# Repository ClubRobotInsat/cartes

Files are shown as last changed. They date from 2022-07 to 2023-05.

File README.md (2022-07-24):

# Cartes du club robot

Toutes les cartes ici sont les cartes en développement au club. Vous pouvez retrouver
dans les release les cartes correspondant à chaque robot.

Dans le dossier `manufactured` vous pouvez retrouver toutes les cartes qui ont été fabriquées. Elles sont
identifiées par un code unique que vous pouvez retrouver sur le PCB.

## Procédure de fabrication

Lorsque vous envoyez une carte à fabriquer, il faut:
- Ajouter un identifiant à la carte (de la forme `[A-Z]{3}`)
- Copier le projet dans le dossier `manufactured`
- Renommer le projet en `[identifiant] {nom}`

Cela permet d'avoir une trace exacte de toutes les cartes fabriquées. Une carte dans le dossier `manufactured` n'est pas
forcément définitive, mais cela permet d'identifier les cartes que nous pouvons trouver dans le local.

## Procédure post-coupe

Lorsque la coupe est finie il faut produire une release contenant toutes les cartes utilisées, c'est pratique pour comprendre
comment fonctionnait le robot.

## Cartes

### Alimentation

Carte principale d'alimentation du robot, adapte la tension batterie pour alimenter les différets composants.

### Base roulante

Carte pour la gestion de la base roulante du robot

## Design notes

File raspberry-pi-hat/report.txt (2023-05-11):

Plotted to '/home/joel/Documents/Code/Club_Robot/cartes/raspberry-pi-hat/raspberry-pi-hat-F_Cu.gbr'.
Plotted to '/home/joel/Documents/Code/Club_Robot/cartes/raspberry-pi-hat/raspberry-pi-hat-B_Cu.gbr'.
Plotted to '/home/joel/Documents/Code/Club_Robot/cartes/raspberry-pi-hat/raspberry-pi-hat-Edge_Cuts.gbr'.
Created Gerber job file '/home/joel/Documents/Code/Club_Robot/cartes/raspberry-pi-hat/raspberry-pi-hat-job.gbrjob'.
Info: Done.

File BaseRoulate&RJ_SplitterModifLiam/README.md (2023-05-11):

# Modif Base Roulante

Suppression d'un via (pour eviter le meme probleme qu'avec la precedente carte)
Rajout de texte, pour meilleure lisibilité
Rajout d'une piste oubliée
Sinon tout à l'air bien

# Modif RJ Splitter

Connexion de tous les +5V
Sinon tout à l'air OK (pour l'instant...)

# Modif carteIO 
Piste oubliée
Via qui me semblait pas être utile étant donné les deux plans de masses correctement mis en place
Probleme : les erreurs d'empreinte des Packs GPIO, je ne sais pas ce que c'est pour l'instant

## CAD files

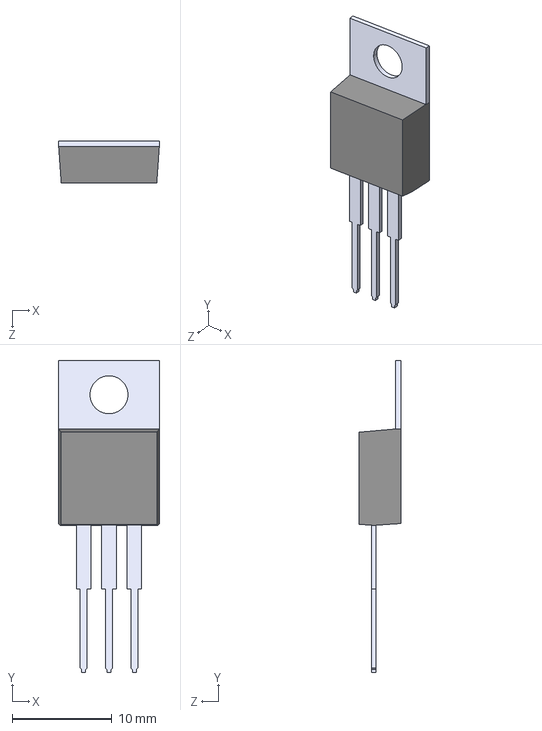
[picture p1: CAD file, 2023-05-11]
BaseRoulate&RJ_SplitterModifLiam/carteIOModifLiam/LM317T_NOPB.step
10.2 x 31.2 x 4.20 mm

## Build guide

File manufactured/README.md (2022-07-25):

| Identifiant | Année | Nom |
|---|---|---|
| AAA |  2022 | Alimentation principale |
| AAB |  2022 | Base roulante |

# Utilité des cartes

## AAA - Alimentation principale

Première version de la carte principale d'alimentation pour le robot. Elle s'alimente avec la batterie et produit du 5V et du 12V régulé. Elle sert également de bouchon pour le bus can.

## AAB - Base roulante

Première version de la base roulante, qui utilse les pont en H makerbot.

## AAC - Prototypage LMD18200

Petit module pour prototyper le module LMD18200 sur breadboard.

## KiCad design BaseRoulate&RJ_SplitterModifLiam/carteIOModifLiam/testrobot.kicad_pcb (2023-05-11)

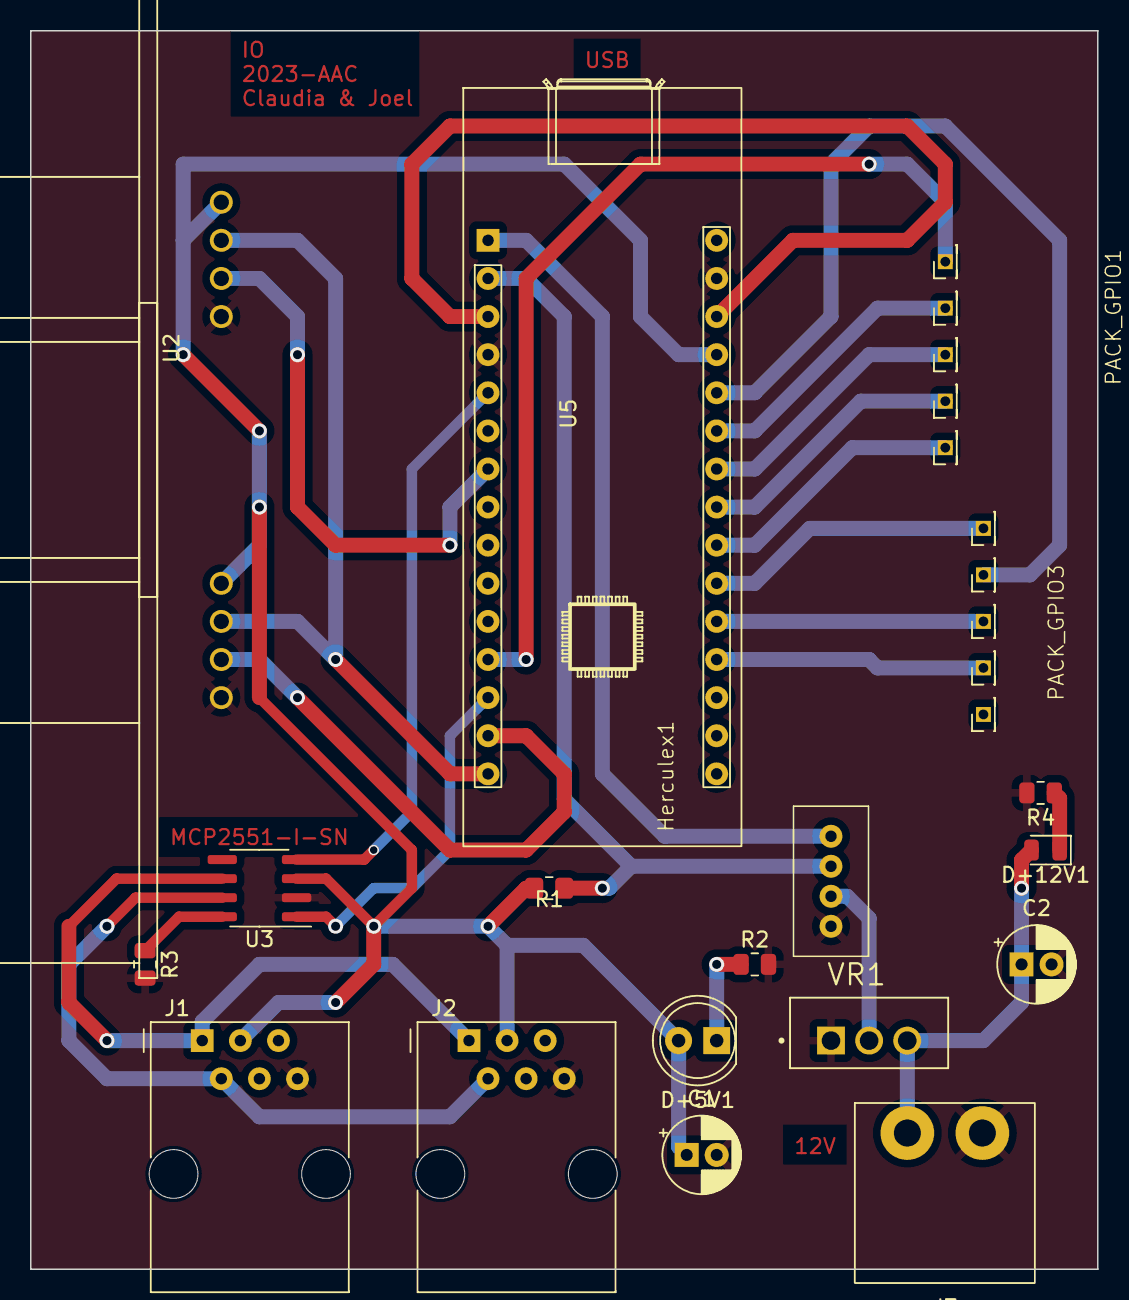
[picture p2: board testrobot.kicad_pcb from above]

Board: 2 copper layers, 71.1 x 82.6 mm, 19 parts (0 on the bottom side), 26 nets.

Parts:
C1: C_Polarized; CP_Radial_D5.0mm_P2.00mm
C2: 470u; CP_Radial_D5.0mm_P2.00mm
D+5V1: LED; LED_D5.0mm
D+12V1: LED bleu; LED_0805_2012Metric
Herculex1: herculex
J1, J2: RJ_can; RJ12
J3: connector_power; WR_TBL_3137_2pins
PACK_GPIO1, PACK_GPIO3: gpio
R1: 4700; R_0805_2012Metric_Pad1.20x1.40mm_HandSolder
R2, R3: R; R_0805_2012Metric
R4: 1k; R_0805_2012Metric
U1, U2: HC-SR04; XCVR_HC-SR04
U3: MCP2551-I-SN; SOIC-8_3.9x4.9mm_P1.27mm
U5: Nucleo_STM32G431KB
VR1: LM317T/NOPB; TO254P1054X470X1955-3

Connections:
+5V: C1.1, D+5V1.2 (A), J1.3 (+5V), J2.3 (+5V), R1.1, U1.1 (VCC), U2.1 (VCC), U3.3 (VDD), U5.27 (+5V)
+8V: Herculex1.2 (+8V), VR1.2 (VOUT)
+12V: C2.1, D+12V1.2 (A), J3.1 (+12V), VR1.3 (VIN)
CANH: J1.2 (CANH), J2.2 (CANH), U3.7 (CANH)
CANL: J1.1 (CANL), J2.1 (CANL), U3.6 (CANL)
CAN_RX: U3.4 (RXD), U5.5 (PA12)
CAN_TX: U3.1 (TXD), U5.13 (PA11)
Echo_b5: U2.3 (ECHO), U5.14 (PB5)
Echo_b7: U1.3 (ECHO), U5.7 (PB7)
GND: C1.2, C2.2, Herculex1.1 (GND), J1.6 (GND), J2.6 (GND), J3.2 (GND), R2.2, R3.2, R4.2, U1.4 (GND), U2.4 (GND), U3.2 (VSS), U5.4 (GND), U5.29 (GND), VR1.1 (ADJ)
unnamed: D+5V1.1 (K), R2.1
unnamed: D+12V1.1 (K), R4.1
unnamed: R3.1, U3.8 (Rs)
unnamed: U5.3 (~RST), U5.28 (~RST)
PA0: PACK_GPIO3.2 (GPIO2), U5.19 (PA0)
PA1: PACK_GPIO3.3 (GPIO3), U5.20 (PA1)
PA2: PACK_GPIO3.4 (GPIO4), U5.26 (PA2)
PA3: PACK_GPIO3.5 (GPIO5), U5.21 (PA3)
PA4: PACK_GPIO1.1 (GPIO1), U5.22 (PA4)
PA5: PACK_GPIO1.2 (GPIO2), U5.23 (PA5/PB7)
PA6: PACK_GPIO1.3 (GPIO3), U5.24 (PA6/PA15)
PA7: PACK_GPIO1.4 (GPIO4), U5.25 (PA7)
PA8: PACK_GPIO1.5 (GPIO5), U5.12 (PA8)
RX_Hercu: Herculex1.4 (RX), U5.1 (PA9)
TX_Herculex: Herculex1.3 (TX), R1.2, U5.2 (PA10)
Trig_b4: U1.2 (TRIG), U2.2 (TRIG), U5.15 (PB4)

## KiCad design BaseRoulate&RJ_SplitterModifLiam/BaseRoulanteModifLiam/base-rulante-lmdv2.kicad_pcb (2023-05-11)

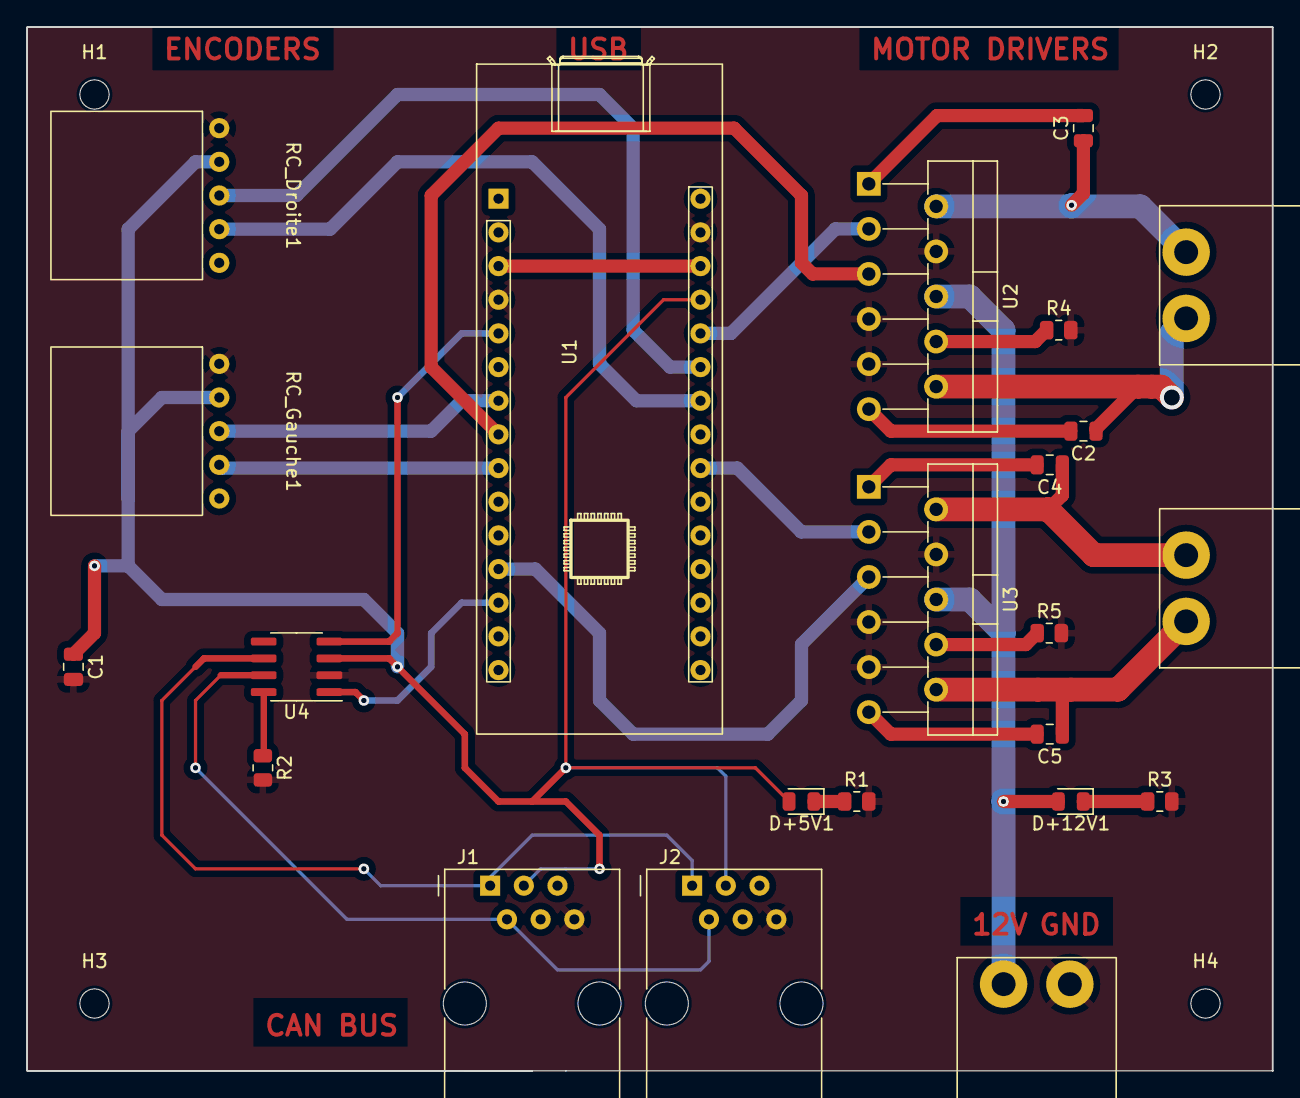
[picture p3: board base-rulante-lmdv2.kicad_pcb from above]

Board: 2 copper layers, 94.0 x 78.7 mm, 27 parts (0 on the bottom side), 29 nets.

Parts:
C1, C2, C3, C4, C5: C_Polarized; C_0805_2012Metric
D+5V1, D+12V1: LED; LED_0805_2012Metric
H1, H2, H3, H4: MountingHole; MountingHole_2.2mm_M2
J1, J2: RJ_can; RJ12
J3, J4, J5: connector_power; WR_TBL_3137_2pins
R1, R2, R3, R4, R5: R; R_0805_2012Metric
RC_Droite1: roues_codeuses; HE14-5-angle
RC_Gauche1: roues_codeuses; HE14-5-angle
U1: Nucleo_STM32G431KB
U2, U3: LMD18200; TO-220-11_P3.4x5.08mm_StaggerOdd_Lead4.85mm_Vertical
U4: MCP2551-I-SN; SOIC-8_3.9x4.9mm_P1.27mm

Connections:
+5V: C1.1, D+5V1.2 (A), J1.3 (+5V), J2.3 (+5V), RC_Droite1.2 (+5V), RC_Gauche1.2 (+5V), U1.27 (+5V), U4.3 (VDD)
+12V: D+12V1.2 (A), J3.1 (+12V), U2.6 (VS), U3.6 (VS)
A_D: RC_Droite1.3 (A), U1.25 (PA7)
A_G: RC_Gauche1.3 (A), U1.7 (PB7)
B_D: RC_Droite1.4 (B), U1.24 (PA6/PA15)
B_G: RC_Gauche1.4 (B), U1.9 (PB6)
CANH: J1.2 (CANH), J2.2 (CANH), U4.7 (CANH)
CANL: J1.1 (CANL), J2.1 (CANL), U4.6 (CANL)
CAN_RX: U1.5 (PA12), U4.4 (RXD)
CAN_TX: U1.13 (PA11), U4.1 (TXD)
DIR_D: U1.26 (PA2), U2.3 (DIRECTION)
DIR_G: U1.22 (PA4), U3.3 (DIRECTION)
GND: C1.2, J1.6 (GND), J2.6 (GND), J3.2 (GND), R1.2, R2.2, R3.2, R4.2, R5.2, RC_Droite1.1 (GND), RC_Gauche1.1 (GND), U1.4 (GND), U1.29 (GND), U2.4 (BRAKE), U2.7 (GND), U2.9 (~THERMAL_FLAG_OUTPUT), U3.4 (BRAKE), U3.7 (GND), U3.9 (~THERMAL_FLAG_OUTPUT), U4.2 (VSS)
Mot_D_Out1: C3.1, J4.2 (GND), U2.2 (OUTPUT1)
Mot_D_Out2: C2.1, J4.1 (+12V), U2.10 (OUTPUT2)
Mot_G_Out1: C4.1, J5.2 (GND), U3.2 (OUTPUT1)
Mot_G_Out2: C5.1, J5.1 (+12V), U3.10 (OUTPUT2)
unnamed: D+5V1.1 (K), R1.1
unnamed: D+12V1.1 (K), R3.1
unnamed: U1.3 (~RST), U1.28 (~RST)
unnamed: C3.2, U2.1 (BOOTSTRAP1)
unnamed: C2.2, U2.11 (BOOTSTRAP2)
unnamed: R4.1, U2.8 (CURRENT_SENSE_OUTPUT)
unnamed: C4.2, U3.1 (BOOTSTRAP1)
unnamed: C5.2, U3.11 (BOOTSTRAP2)
unnamed: R5.1, U3.8 (CURRENT_SENSE_OUTPUT)
unnamed: R2.1, U4.8 (Rs)
PWM_D: U1.8 (PA15), U2.5 (PWM)
PWM_G: U1.12 (PA8), U3.5 (PWM)

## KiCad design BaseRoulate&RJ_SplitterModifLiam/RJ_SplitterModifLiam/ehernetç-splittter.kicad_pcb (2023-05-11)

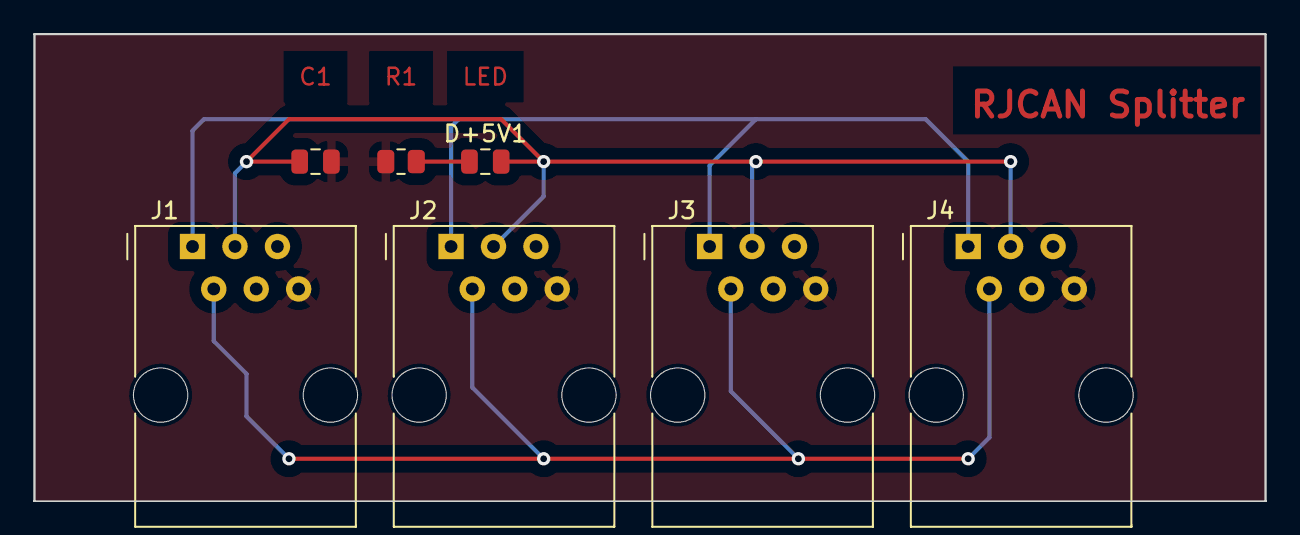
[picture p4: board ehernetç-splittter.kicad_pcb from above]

Board: 2 copper layers, 73.7 x 27.9 mm, 7 parts (0 on the bottom side), 5 nets.

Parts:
C1: C_Polarized; C_0805_2012Metric
D+5V1: LED; C_0805_2012Metric
J1, J2, J3, J4: RJ_can; RJ12
R1: R; R_0805_2012Metric

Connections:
+5V: C1.1, D+5V1.2 (A), J1.3 (+5V), J2.3 (+5V), J3.3 (+5V), J4.3 (+5V)
CANH: J1.2 (CANH), J2.2 (CANH), J3.2 (CANH), J4.2 (CANH)
CANL: J1.1 (CANL), J2.1 (CANL), J3.1 (CANL), J4.1 (CANL)
GND: C1.2, J1.6 (GND), J2.6 (GND), J3.6 (GND), J4.6 (GND), R1.2
unnamed: D+5V1.1 (K), R1.1

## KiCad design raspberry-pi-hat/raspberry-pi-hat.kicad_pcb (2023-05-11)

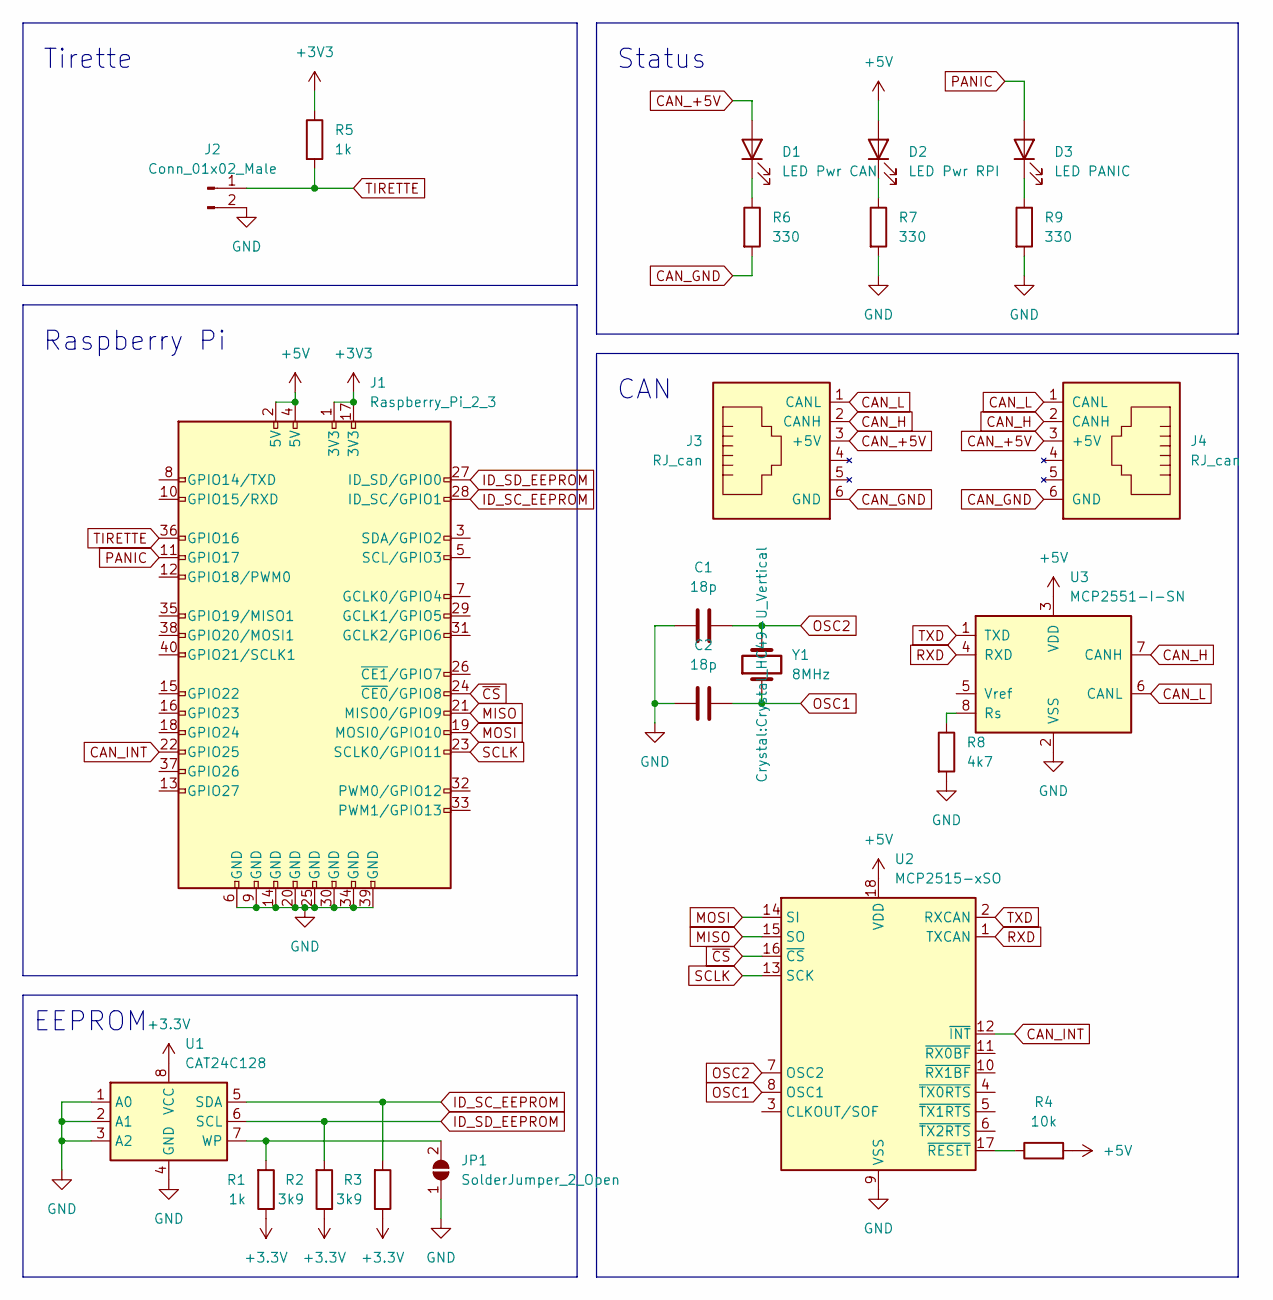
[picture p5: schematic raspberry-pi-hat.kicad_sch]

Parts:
C1, C2: 18p; C_0805_2012Metric
D1: LED Pwr CAN; LED_0805_2012Metric
D2: LED Pwr RPI; LED_0805_2012Metric
D3: LED PANIC; LED_0805_2012Metric
J1: Raspberry_Pi_2_3; PinHeader_2x20_P2.54mm_Vertical
J2: Conn_01x02_Male; PinHeader_1x02_P2.54mm_Horizontal
J3, J4: RJ_can; RJ12
JP1: SolderJumper_2_Open; SolderJumper-2_P1.3mm_Open_TrianglePad1.0x1.5mm
R1, R5: 1k; R_0805_2012Metric
R2, R3: 3k9; R_0805_2012Metric
R4: 10k; R_0805_2012Metric
R6, R7, R9: 330; R_0805_2012Metric
R8: 4k7; R_0805_2012Metric
U1: CAT24C128; SOIC-8_3.9x4.9mm_P1.27mm
U2: MCP2515-xSO; SOIC-18W_7.5x11.6mm_P1.27mm
U3: MCP2551-I-SN; SOIC-8_3.9x4.9mm_P1.27mm
Y1: 8MHz; Crystal_HC49-U_Vertical

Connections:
+3.3V: R1.1, R2.1, R3.1, U1.8 (VCC)
+3V3: J1.1 (3V3), J1.17 (3V3), R5.1
+5V: D2.2 (A), J1.2 (5V), J1.4 (5V), R4.2, U2.18 (VDD), U3.3 (VDD)
CAN_+5V: D1.2 (A), J3.3 (+5V), J4.3 (+5V)
CAN_GND: J3.6 (GND), J4.6 (GND), R6.2
CAN_H: J3.2 (CANH), J4.2 (CANH), U3.7 (CANH)
CAN_INT: J1.22 (GPIO25), U2.12 (~INT)
CAN_L: J3.1 (CANL), J4.1 (CANL), U3.6 (CANL)
GND: C1.2, C2.1, J1.6 (GND), J1.9 (GND), J1.14 (GND), J1.20 (GND), J1.25 (GND), J1.30 (GND), J1.34 (GND), J1.39 (GND), J2.2, JP1.1 (A), R7.2, R8.2, R9.2, U1.1 (A0), U1.2 (A1), U1.3 (A2), U1.4 (GND), U2.9 (VSS), U3.2 (VSS)
ID_SC_EEPROM: J1.28 (ID_SC/GPIO1), R3.2, U1.5 (SDA)
ID_SD_EEPROM: J1.27 (ID_SD/GPIO0), R2.2, U1.6 (SCL)
MISO: J1.21 (MISO0/GPIO9), U2.15 (SO)
MOSI: J1.19 (MOSI0/GPIO10), U2.14 (SI)
unnamed: D1.1 (K), R6.1
unnamed: D2.1 (K), R7.1
unnamed: D3.1 (K), R9.1
unnamed: JP1.2 (B), R1.2, U1.7 (WP)
unnamed: R4.1, U2.17 (~RESET)
unnamed: R8.1, U3.8 (Rs)
OSC1: C2.2, U2.8 (OSC1), Y1.1
OSC2: C1.1, U2.7 (OSC2), Y1.2
PANIC: D3.2 (A), J1.11 (GPIO17)
RXD: U2.1 (TXCAN), U3.4 (RXD)
SCLK: J1.23 (SCLK0/GPIO11), U2.13 (SCK)
TIRETTE: J1.36 (GPIO16), J2.1, R5.2
TXD: U2.2 (RXCAN), U3.1 (TXD)
~CS: J1.24 (~CE0/GPIO8), U2.16 (~CS)

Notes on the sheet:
Status
Raspberry Pi
EEPROM
Tirette
CAN

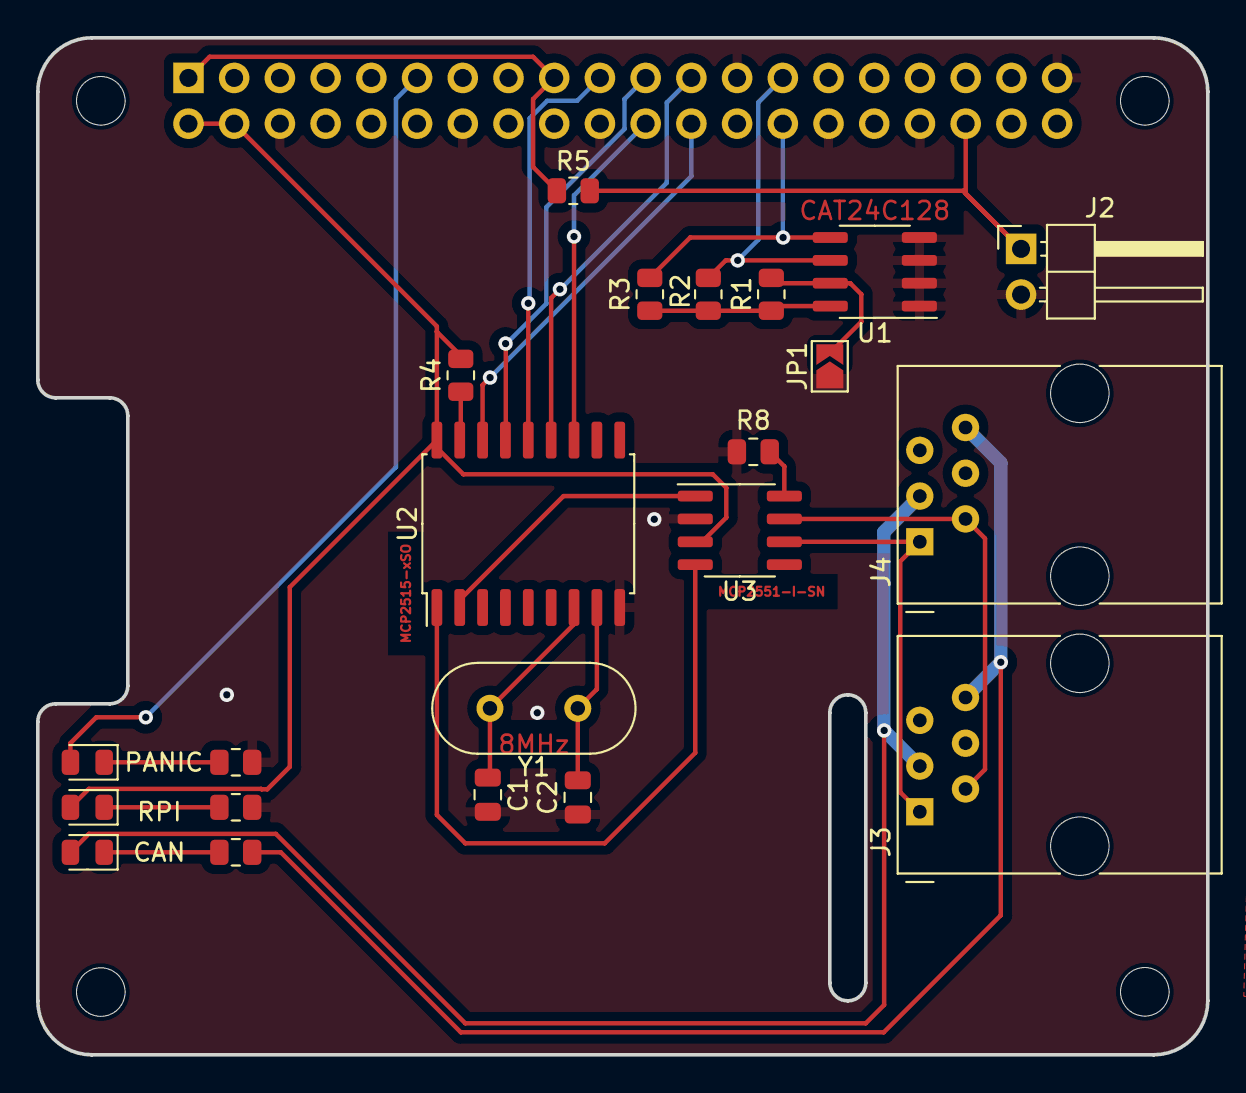
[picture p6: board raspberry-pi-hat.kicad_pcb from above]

Board: 2 copper layers, 65.0 x 56.5 mm, 27 parts (1 on the bottom side), 27 nets.

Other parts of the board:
M1, M2, M3, M4: MountingHole_2.7mm

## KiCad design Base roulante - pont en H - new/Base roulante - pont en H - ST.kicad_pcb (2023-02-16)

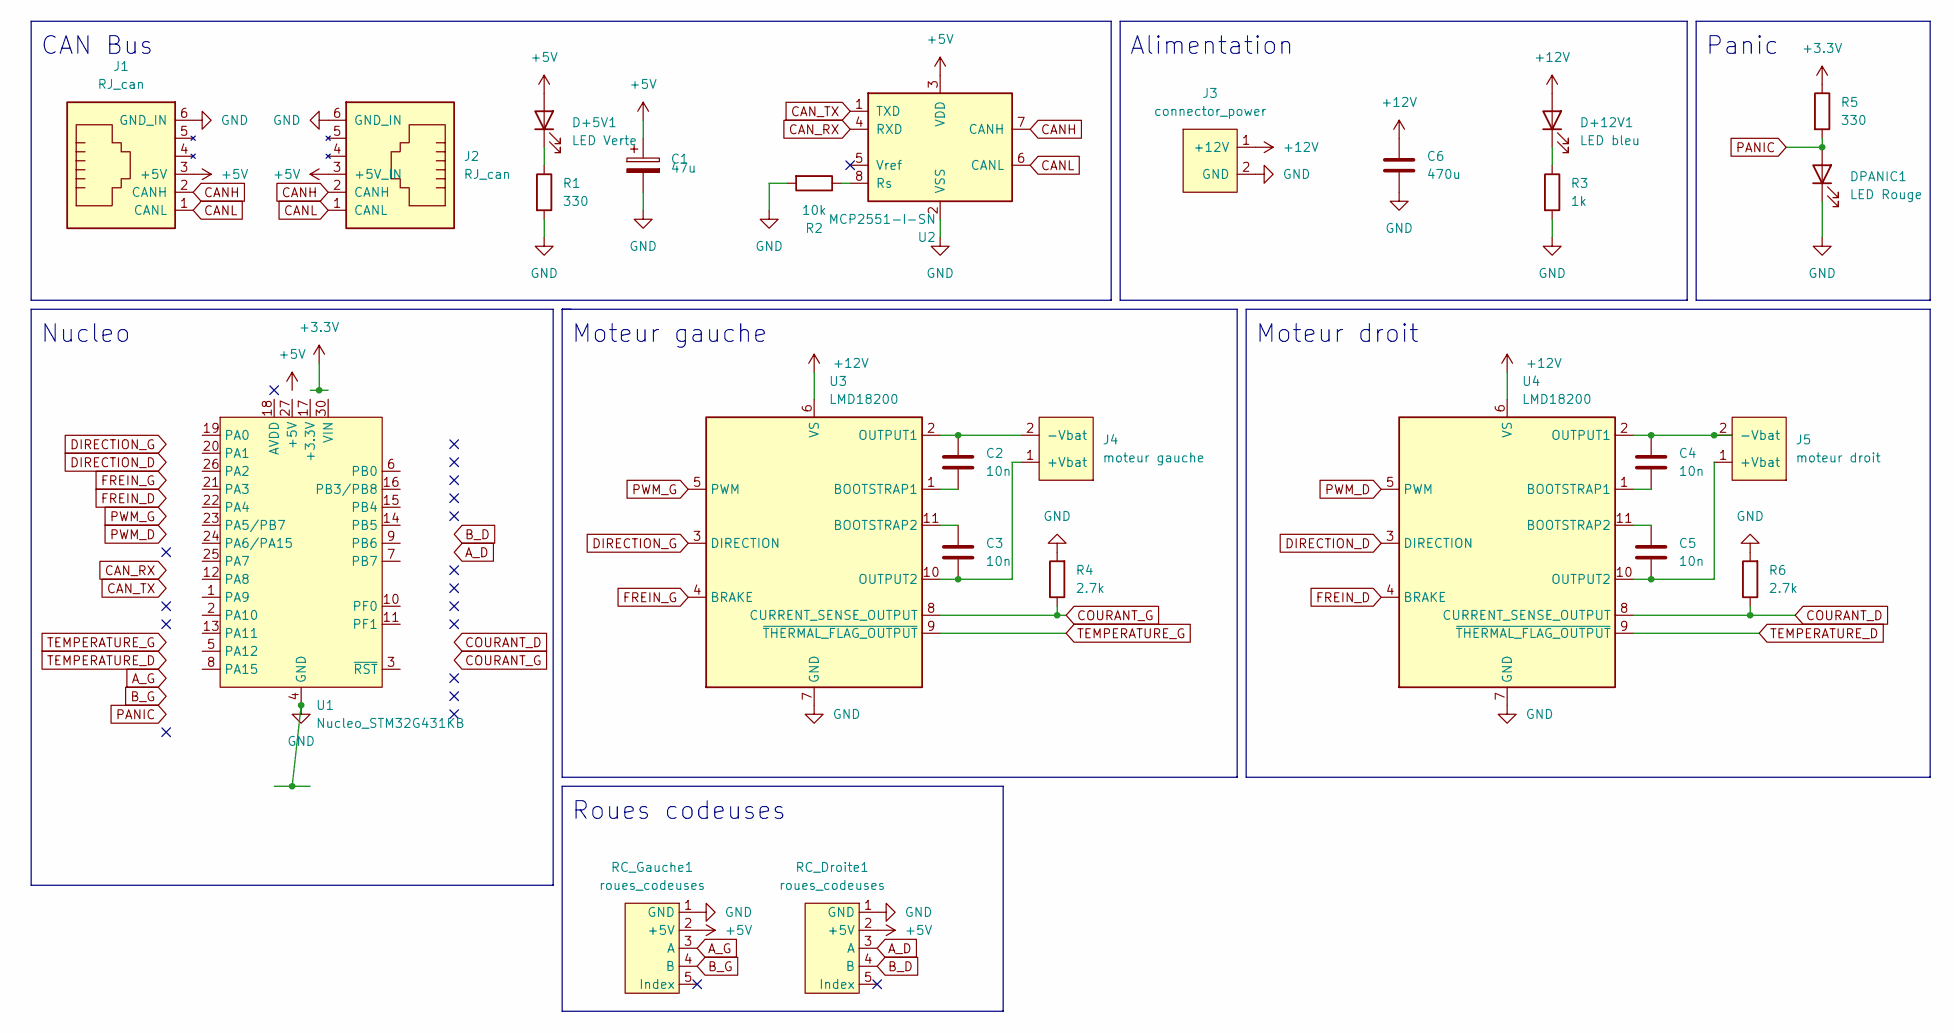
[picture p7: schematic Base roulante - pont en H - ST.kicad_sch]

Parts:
C1: 47u; CP_Radial_D5.0mm_P2.00mm
C2, C3, C4, C5: 10n; C_0805_2012Metric
C6: 470u; CP_Radial_D8.0mm_P3.50mm
D+5V1: LED Verte; LED_0805_2012Metric
D+12V1: LED bleu; LED_0805_2012Metric
DPANIC1: LED Rouge; LED_0805_2012Metric
J1, J2: RJ_can; RJ12
J3: connector_power; WR_TBL_3137_2pins
J4: moteur gauche; WR_TBL_3137_2pins
J5: moteur droit; WR_TBL_3137_2pins
R1, R5: 330; R_0805_2012Metric
R2: 10k; R_0805_2012Metric
R3: 1k; R_0805_2012Metric
R4, R6: 2.7k; R_0805_2012Metric
RC_Droite1: roues_codeuses; HE14-5-angle
RC_Gauche1: roues_codeuses; HE14-5-angle
U1: Nucleo_STM32G431KB
U2: MCP2551-I-SN; SOIC-8_3.9x4.9mm_P1.27mm
U3, U4: LMD18200; TO-220-11_P3.4x5.08mm_StaggerOdd_Lead4.85mm_Vertical

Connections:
+3.3V: R5.1
+5V: C1.1, D+5V1.2 (A), J1.3 (+5V), J2.3 (+5V_IN), RC_Droite1.2 (+5V), RC_Gauche1.2 (+5V), U2.3 (VDD)
+12V: C6.1, D+12V1.2 (A), J3.1 (+12V), U3.6 (VS), U4.6 (VS)
A_D: RC_Droite1.3 (A)
A_G: RC_Gauche1.3 (A)
B_D: RC_Droite1.4 (B)
B_G: RC_Gauche1.4 (B)
CANH: J1.2 (CANH), J2.2 (CANH), U2.7 (CANH)
CANL: J1.1 (CANL), J2.1 (CANL), U2.6 (CANL)
CAN_RX: U2.4 (RXD)
CAN_TX: U2.1 (TXD)
COURANT_D: R6.1, U4.8 (CURRENT_SENSE_OUTPUT)
COURANT_G: R4.1, U3.8 (CURRENT_SENSE_OUTPUT)
DIRECTION_D: U4.3 (DIRECTION)
DIRECTION_G: U3.3 (DIRECTION)
FREIN_D: U4.4 (BRAKE)
FREIN_G: U3.4 (BRAKE)
GND: C1.2, C6.2, DPANIC1.1 (K), J1.6 (GND_IN), J2.6 (GND_IN), J3.2 (GND), R1.2, R2.2, R3.2, R4.2, R6.2, RC_Droite1.1 (GND), RC_Gauche1.1 (GND), U1.4 (GND), U1.29 (GND), U2.2 (VSS), U3.7 (GND), U4.7 (GND)
unnamed: C2.1, J4.2 (-Vbat), U3.2 (OUTPUT1)
unnamed: C2.2, U3.1 (BOOTSTRAP1)
unnamed: C3.1, U3.11 (BOOTSTRAP2)
unnamed: C3.2, J4.1 (+Vbat), U3.10 (OUTPUT2)
unnamed: C4.1, J5.2 (-Vbat), U4.2 (OUTPUT1)
unnamed: C4.2, U4.1 (BOOTSTRAP1)
unnamed: C5.1, U4.11 (BOOTSTRAP2)
unnamed: C5.2, J5.1 (+Vbat), U4.10 (OUTPUT2)
unnamed: D+5V1.1 (K), R1.1
unnamed: D+12V1.1 (K), R3.1
unnamed: R2.1, U2.8 (Rs)
unnamed: U1.3 (~RST), U1.28 (~RST)
PANIC: DPANIC1.2 (A), R5.2
PWM_D: U4.5 (PWM)
PWM_G: U3.5 (PWM)
TEMPERATURE_D: U4.9 (~THERMAL_FLAG_OUTPUT)
TEMPERATURE_G: U3.9 (~THERMAL_FLAG_OUTPUT)

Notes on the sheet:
Panic
Alimentation
CAN Bus
Moteur droit
Roues codeuses
Moteur gauche
Nucleo

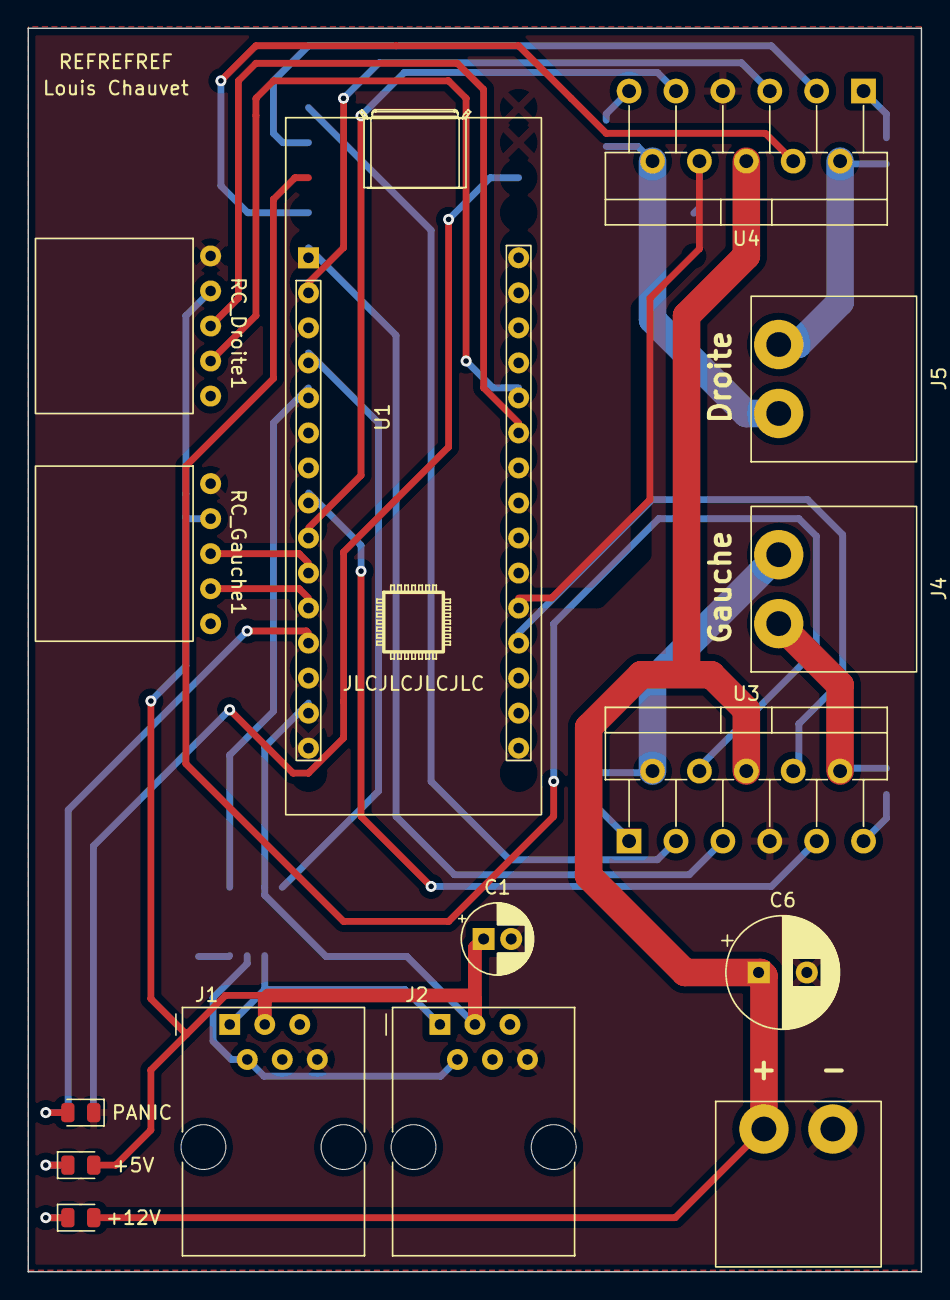
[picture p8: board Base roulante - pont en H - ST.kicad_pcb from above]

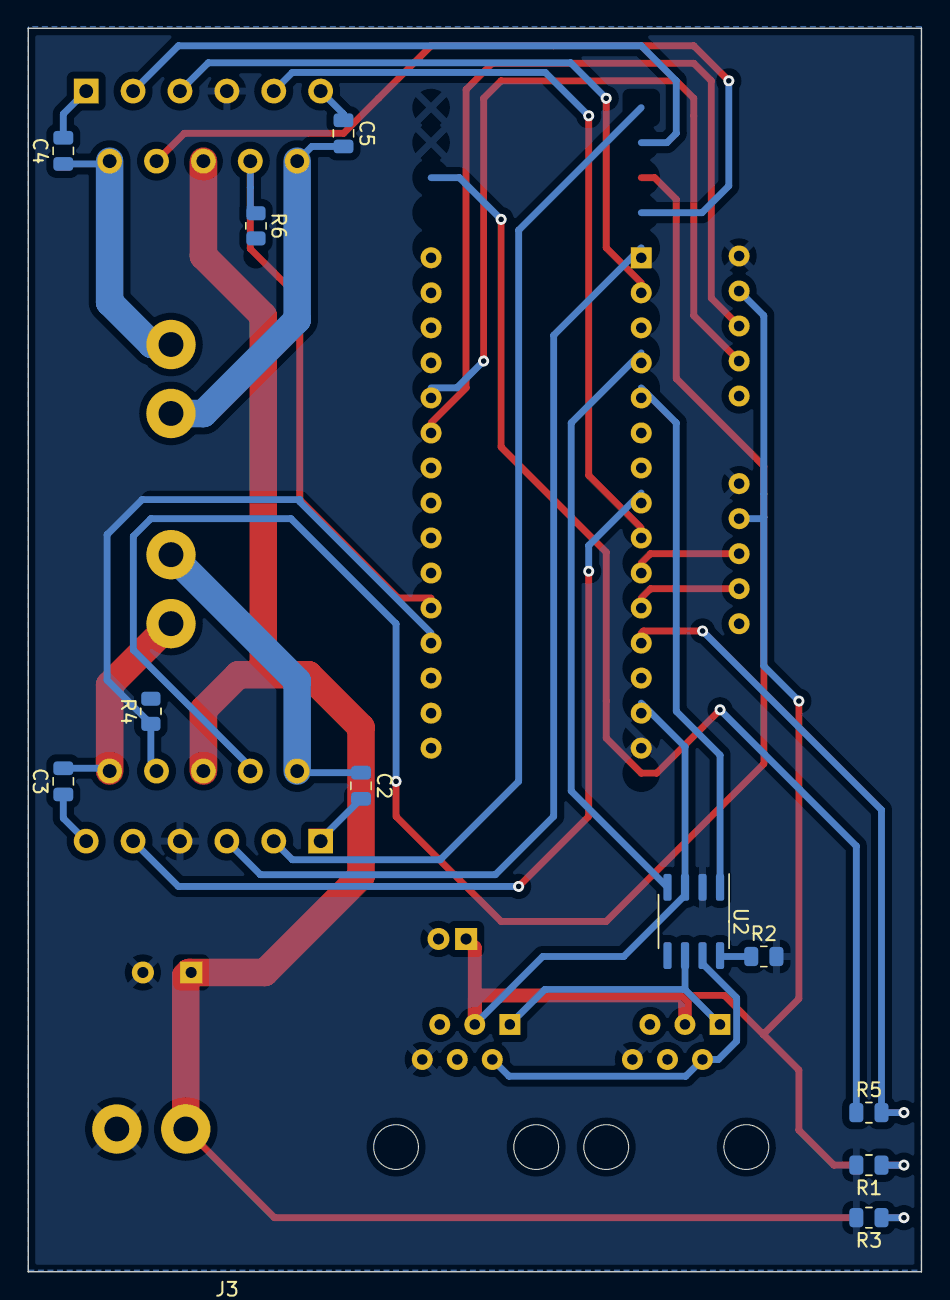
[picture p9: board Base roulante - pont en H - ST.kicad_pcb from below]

Board: 2 copper layers, 64.8 x 90.2 mm, 26 parts (11 on the bottom side), 20 nets.

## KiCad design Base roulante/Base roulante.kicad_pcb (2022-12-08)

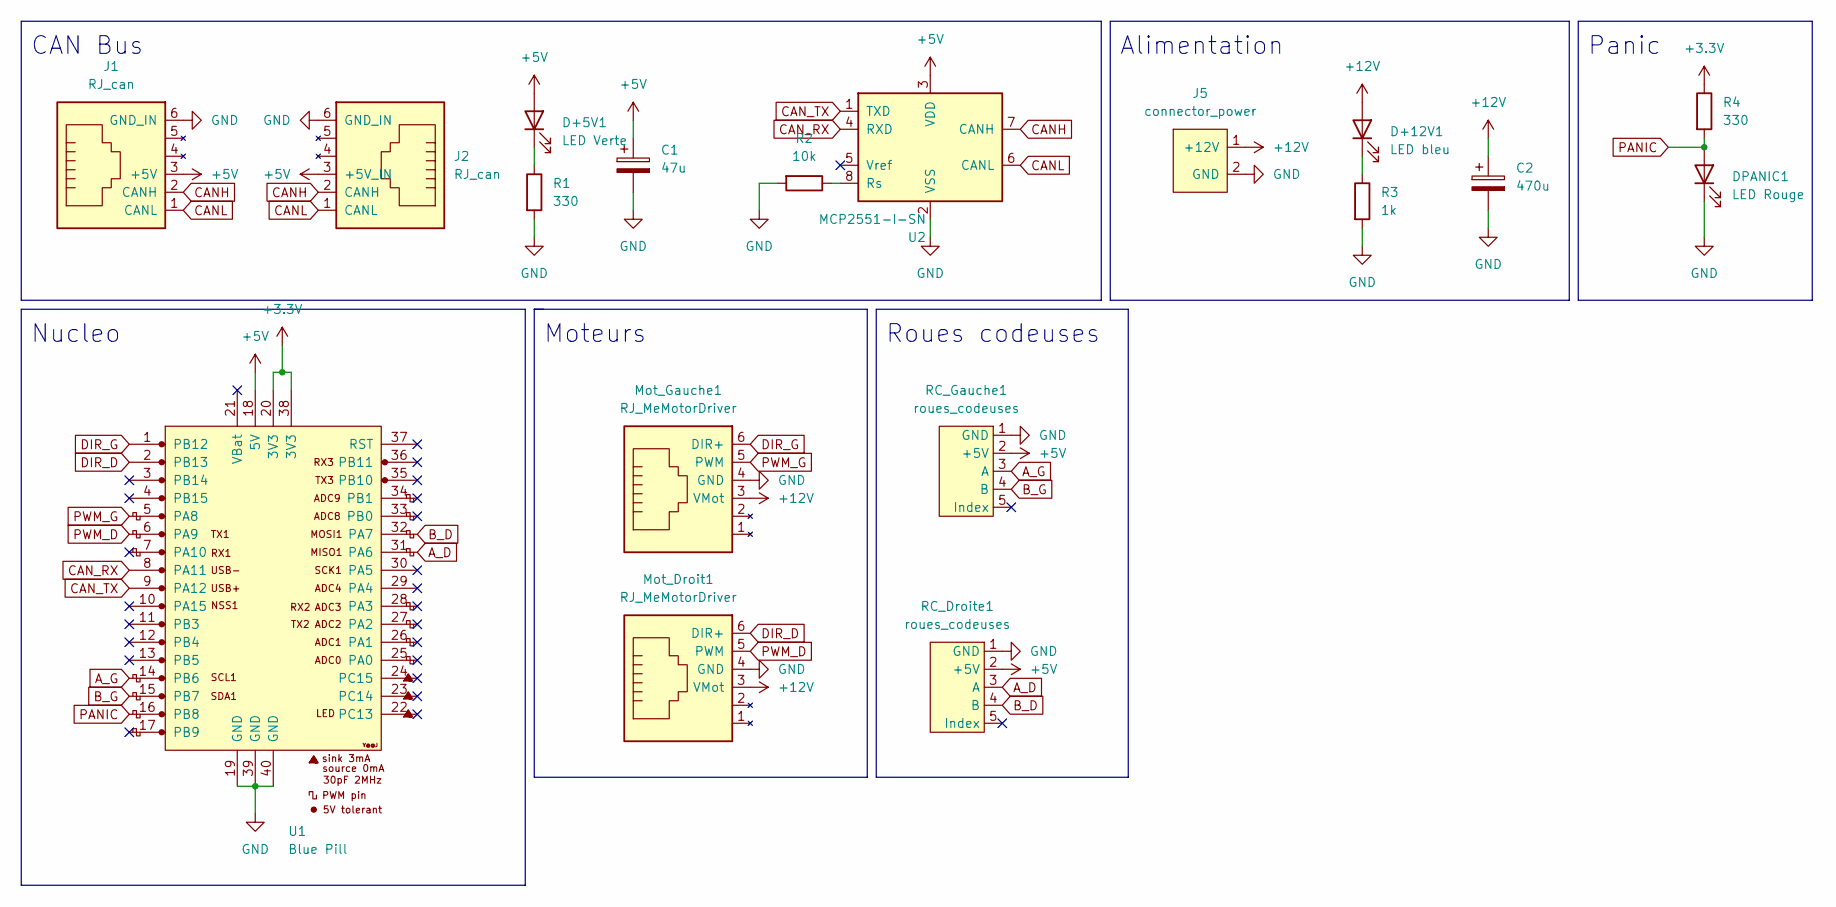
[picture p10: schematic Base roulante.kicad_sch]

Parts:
C1: 47u; CP_Radial_D5.0mm_P2.00mm
C2: 470u; CP_Radial_D5.0mm_P2.00mm
D+5V1: LED Verte; LED_0805_2012Metric
D+12V1: LED bleu; LED_0805_2012Metric
DPANIC1: LED Rouge; LED_0805_2012Metric
J1, J2: RJ_can; RJ12
J5: connector_power; WR_TBL_3137_2pins
Mot_Droit1: RJ_MeMotorDriver; RJ12
Mot_Gauche1: RJ_MeMotorDriver; RJ12
R1, R4: 330; R_0805_2012Metric
R2: 10k; R_0805_2012Metric
R3: 1k; R_0805_2012Metric
RC_Droite1: roues_codeuses; HE14-5-angle
RC_Gauche1: roues_codeuses; HE14-5-angle
U1: Blue Pill
U2: MCP2551-I-SN; SOIC-8_3.9x4.9mm_P1.27mm

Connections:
+3.3V: R4.1, U1.20 (3V3), U1.38 (3V3)
+5V: C1.1, D+5V1.2 (A), J1.3 (+5V), J2.3 (+5V_IN), RC_Droite1.2 (+5V), RC_Gauche1.2 (+5V), U1.18 (5V), U2.3 (VDD)
+12V: C2.1, D+12V1.2 (A), J5.1 (+12V), Mot_Droit1.3 (VMot), Mot_Gauche1.3 (VMot)
A_D: RC_Droite1.3 (A), U1.31 (PA6)
A_G: RC_Gauche1.3 (A), U1.14 (PB6)
B_D: RC_Droite1.4 (B), U1.32 (PA7)
B_G: RC_Gauche1.4 (B), U1.15 (PB7)
CANH: J1.2 (CANH), J2.2 (CANH), U2.7 (CANH)
CANL: J1.1 (CANL), J2.1 (CANL), U2.6 (CANL)
CAN_RX: U1.8 (PA11), U2.4 (RXD)
CAN_TX: U1.9 (PA12), U2.1 (TXD)
DIR_D: Mot_Droit1.6 (DIR+), U1.2 (PB13)
DIR_G: Mot_Gauche1.6 (DIR+), U1.1 (PB12)
GND: C1.2, C2.2, DPANIC1.1 (K), J1.6 (GND_IN), J2.6 (GND_IN), J5.2 (GND), Mot_Droit1.4 (GND), Mot_Gauche1.4 (GND), R1.2, R2.2, R3.2, RC_Droite1.1 (GND), RC_Gauche1.1 (GND), U1.19 (GND), U1.39 (GND), U1.40 (GND), U2.2 (VSS)
unnamed: D+5V1.1 (K), R1.1
unnamed: D+12V1.1 (K), R3.1
unnamed: R2.1, U2.8 (Rs)
PANIC: DPANIC1.2 (A), R4.2, U1.16 (PB8)
PWM_D: Mot_Droit1.5 (PWM), U1.6 (PA9)
PWM_G: Mot_Gauche1.5 (PWM), U1.5 (PA8)

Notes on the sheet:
Alimentation
Nucleo
CAN Bus
Roues codeuses
Panic
Moteurs

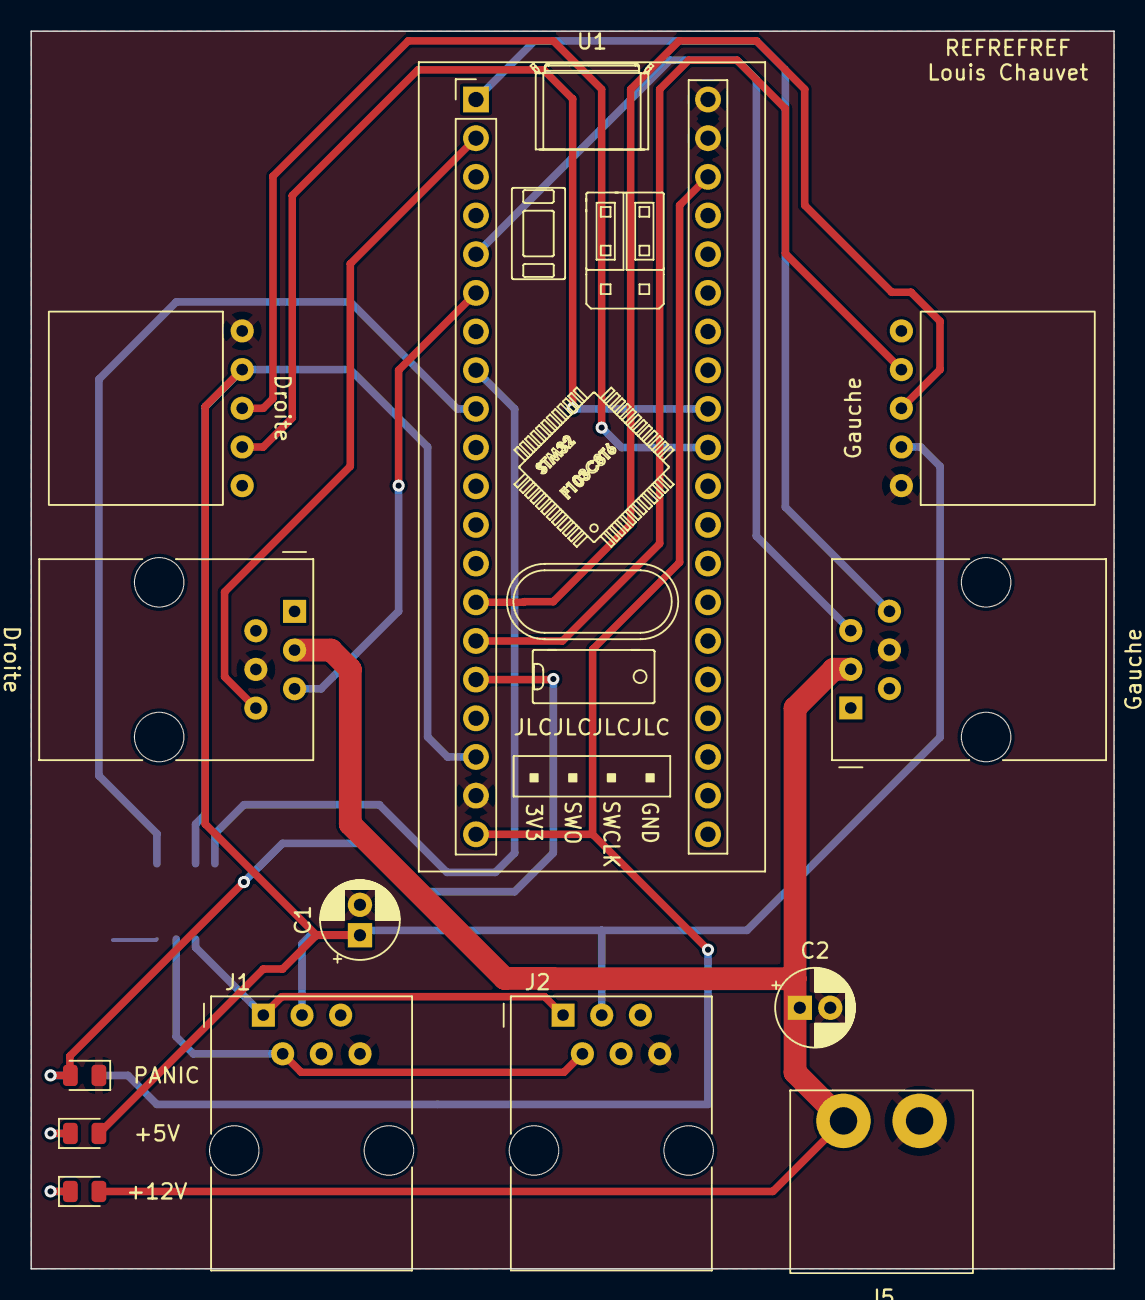
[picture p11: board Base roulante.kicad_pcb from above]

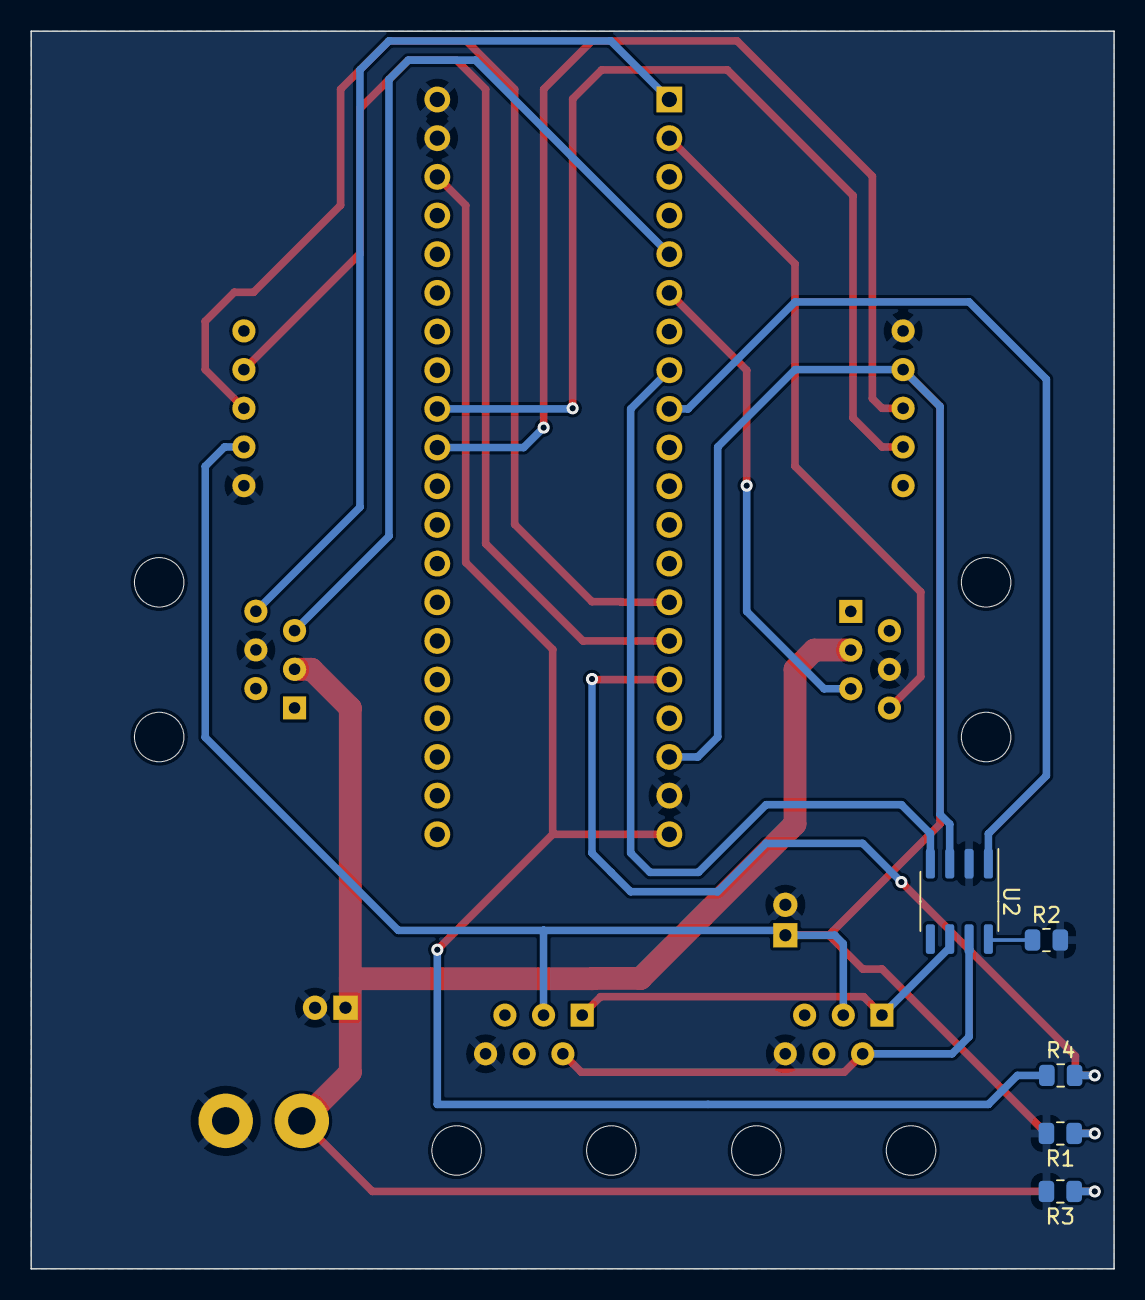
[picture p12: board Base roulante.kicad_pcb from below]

Board: 2 copper layers, 71.1 x 81.3 mm, 18 parts (5 on the bottom side), 20 nets.

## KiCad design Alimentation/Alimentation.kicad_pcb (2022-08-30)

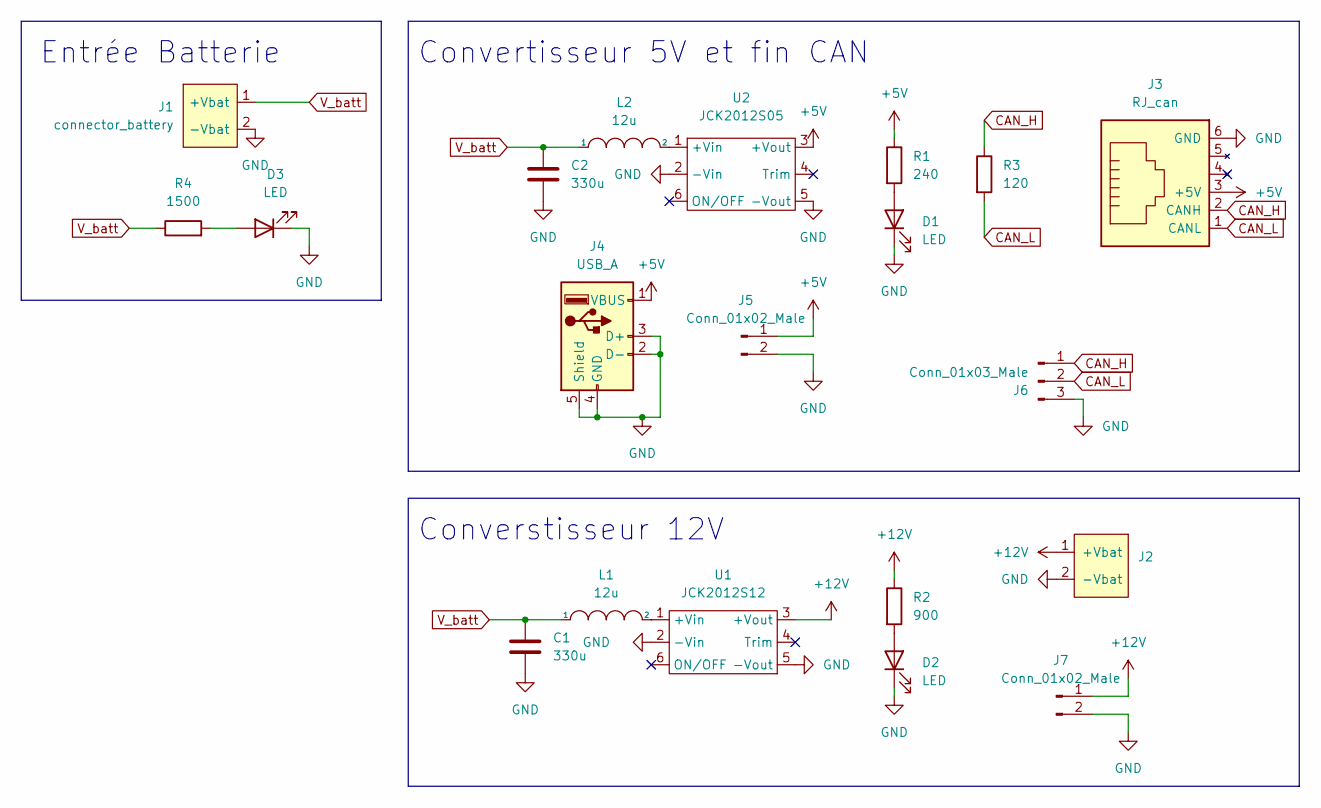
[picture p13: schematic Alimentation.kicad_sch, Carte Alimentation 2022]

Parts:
C1, C2: 330u; CP_Radial_D7.5mm_P2.50mm
D1, D2, D3: LED; LED_D5.0mm
J1: connector_battery; WR_TBL_3137_2pins
J2: WR_TBL_3137_2pins
J3: RJ_can; RJ12
J4: USB_A
J5, J7: Conn_01x02_Male; PinHeader_1x02_P2.54mm_Horizontal
J6: Conn_01x03_Male; PinHeader_1x03_P2.54mm_Horizontal
L1, L2: 12u; L_Radial_D7.8mm_P5.00mm_Fastron_07HCP
R1: 240; R_0805_2012Metric_Pad1.20x1.40mm_HandSolder
R2: 900; R_0805_2012Metric_Pad1.20x1.40mm_HandSolder
R3: 120; R_0805_2012Metric_Pad1.20x1.40mm_HandSolder
R4: 1500; R_0805_2012Metric_Pad1.20x1.40mm_HandSolder
U1: JCK2012S12; JCK
U2: JCK2012S05; JCK

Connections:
+5V: J3.3 (+5V), J4.1 (VBUS), J5.1, R1.1, U2.3 (+Vout)
+12V: J2.1 (+Vbat), J7.1, R2.1, U1.3 (+Vout)
CAN_H: J3.2 (CANH), J6.1, R3.1
CAN_L: J3.1 (CANL), J6.2, R3.2
GND: C1.2, C2.2, D1.1 (K), D2.1 (K), D3.1 (K), J1.2 (-Vbat), J2.2 (-Vbat), J3.6 (GND), J4.2 (D-), J4.3 (D+), J4.4 (GND), J4.5 (Shield), J5.2, J6.3, J7.2, U1.2 (-Vin), U1.5 (-Vout), U2.2 (-Vin), U2.5 (-Vout)
unnamed: D1.2 (A), R1.2
unnamed: D2.2 (A), R2.2
unnamed: D3.2 (A), R4.2
unnamed: L1.2, U1.1 (+Vin)
unnamed: L2.2, U2.1 (+Vin)
V_batt: C1.1, C2.1, J1.1 (+Vbat), L1.1, L2.1, R4.1

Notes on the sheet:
Convertisseur 5V et fin CAN
Converstisseur 12V
Entrée Batterie



Board: 2 copper layers, 63.5 x 99.1 mm, 20 parts (4 on the bottom side), 11 nets.

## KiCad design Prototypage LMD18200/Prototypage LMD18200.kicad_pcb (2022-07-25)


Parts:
J1, J2: Conn_01x06; PinHeader_1x06_P2.54mm_Vertical
U1: LMD18200; TO-220-11_P3.4x5.08mm_StaggerOdd_Lead4.85mm_Vertical

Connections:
BOOTSTRAP1: J2.6, U1.1 (BOOTSTRAP1)
BOOTSTRAP2: J2.1, U1.11 (BOOTSTRAP2)
BRAKE: J1.2, U1.4 (BRAKE)
CURRENT_SENSE_OUTPUT: J1.4, U1.8 (CURRENT_SENSE_OUTPUT)
DIRECTION: J2.5, U1.3 (DIRECTION)
GND: J2.3, U1.7 (GND)
OUTPUT1: J1.1, U1.2 (OUTPUT1)
OUTPUT2: J1.5, U1.10 (OUTPUT2)
PWM: J2.4, U1.5 (PWM)
VS: J1.3, U1.6 (VS)
~THERMAL_SENSE_OUTPUT: J2.2, U1.9 (~THERMAL_FLAG_OUTPUT)


Board: 2 copper layers, 24.8 x 21.0 mm, 3 parts (0 on the bottom side), 11 nets.

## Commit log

2022-07-20 Ajout de la led
    [Alimentation.kicad_pcb, Alimentation.kicad_sch]
2022-07-23 Update alimentation; Add Base roulante
    [Alimentation.kicad_pcb, Alimentation.kicad_sch, Base roulante.kicad_pcb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]
2022-07-24 Update base roulante
    [Base roulante.kicad_pcb, Base roulante.kicad_sch]
2022-08-30 Update card to cut board near to the connector
    [Alimentation.kicad_pcb, Base roulante.kicad_pcb]
2022-12-08 Add Base roulante updated
    [Base roulante - pont en H.kicad_pcb, Base roulante - pont en H.kicad_sch, Base roulante.kicad_pcb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]
2023-02-16 Avant de partir je donne tout
    [Base roulante - pont en H - ST.kicad_pcb, Base roulante - pont en H - ST.kicad_sch]
2023-03-25 Ajout de la première version du hat
    [raspberry-pi-hat.kicad_pcb, raspberry-pi-hat.kicad_sch]
2023-05-11 rjcan split
    [base-rulante-lmdv2.kicad_pcb, base-rulante-lmdv2.kicad_sch, ehernetç-splittter.kicad_pcb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]
2023-05-11 base roulante reroute au cas ou
    [base-rulante-lmdv2.kicad_pcb, base-rulante-lmdv2.kicad_sch]
2023-05-11 Modifs proposés par Liam
    J'ai enleve un via et j'ai rajouter du texte sur la carte, il manque juste une reference avec NOM#Num
    [base-rulante-lmdv2.kicad_pcb, base-rulante-lmdv2.kicad_sch]
2023-05-11 carte IO
    [LM317T_NOPB.step, base-rulante-lmdv2.kicad_pcb, testrobot.kicad_pcb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]
2023-05-11 Modifications apportées aux dernières cartes
    [base-rulante-lmdv2.kicad_pcb, base-rulante-lmdv2.kicad_sch, ehernetç-splittter.kicad_pcb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]
2023-05-11 Modif de la carteIO
    [LM317T_NOPB.step, testrobot.kicad_pcb, testrobot.kicad_sch]
2023-05-12 added some vias for the grownd plain
    [base-rulante-lmdv2.kicad_pcb, ehernetç-splittter.kicad_pcb, testrobot.kicad_pcb]
2023-10-09 Fichiers de la base roulante pour 2024
    [Base_Roulante_2024.kicad_pcb, Base_Roulante_2024.kicad_sch]
2023-10-09 Mise à jour du schema pour inclure certains blocs
    [Base_Roulante_2024.kicad_pcb, Base_Roulante_2024.kicad_sch]
2023-10-14 J'ai changé la carte Base Roulante pour n'avoir qu'un driver et des interfaces
    [Base_Roulante_2024.kicad_sch]
2023-11-09 Update Base_Roulante_2024
    [Base_Roulante_2024.kicad_sch]
2023-11-12 Added the schematic with use of hierachy
    Top_level_schematic is the "main" schematic, with stepper_motor_driver as a sub-schematic. Both need to be in the same folder to work.
    [Stepper_motor_driver.kicad_sch, Top_level_schematic.kicad_sch]
2023-12-21 Created folder for the H bridge motor driver schematics
2023-12-21 Added top level schematic and H bridge schematic.
    Top level schematic is the main schematic, the other files contain the required schematics for using hierarchical sheets.
    [Base_Roulante_Top-Level.kicad_sch, PontH_2023-24.kicad_sch]
